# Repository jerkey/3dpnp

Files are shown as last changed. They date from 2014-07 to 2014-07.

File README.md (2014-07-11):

rotatorbracket.scad is for mounting a 6403R200 hollow-shaft motor on the right side of a 2014 type a machine http://typeamachines.com
the bracket fits on the bottom edge of the circuitboard using 18mm long screws to replace the original screws that held the board in place.
the Vcc Out connector can't be used as the connector is covering it up.  solder to the back of the board if you need Vcc out.

a 3.15mm tube is shoved through the motor and fits through the hole of the bracket, where a vacuum hose is attached.  A piece of heat shrink or two go around the lower end of the tube so that the vacuum pick and place needle can be shoved on and stays centered.

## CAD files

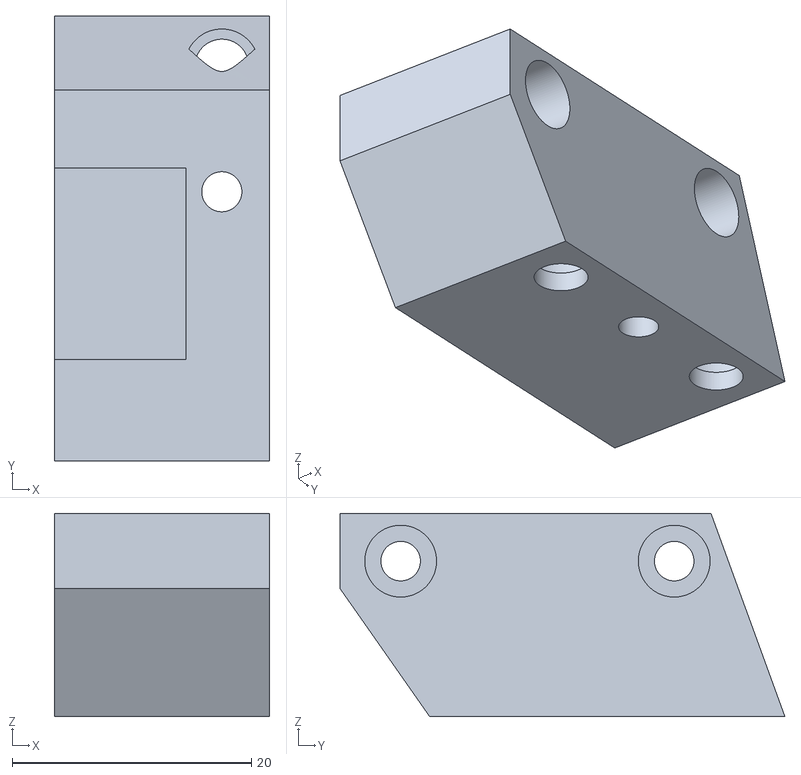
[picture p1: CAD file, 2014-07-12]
rotatorbracket.stl
18.0 x 37.2 x 17.0

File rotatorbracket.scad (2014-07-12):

$fn=100;
pipeDia = 3.35;
blockY = 33;
blockZ = 17;
blockX = 18;
motorCenterX = 14; // X line of motor posts and shaft
motorOffsetY = 6; // move the motor +Y this much relative to center

boardScrewSpacing = 25.4*0.9; // screws are 0.9" apart
screwHoleDia = 3.3; // M3 screw thread clearance tunnel
screwHeadDia = 6; // M3 screw head clearance tunnel

difference() {
  translate([0,blockY/-2,0]) cube([blockX,blockY+motorOffsetY,blockZ]);
  translate([motorCenterX,motorOffsetY,-0.1]) cylinder(r = pipeDia/2, h = blockZ+.2); // pipe hole
  translate([motorCenterX,21/2+motorOffsetY,-0.1]) cylinder(r = 4.5/2, h = 2); // motor nub holes (drill to 4.3mm)
  translate([motorCenterX,-21/2+motorOffsetY,-0.1]) cylinder(r = 4.5/2, h = 2);
  translate([motorCenterX,21/2+motorOffsetY,1.7]) cylinder(r = 6.2/2, h = 6); // motor nub larger part
  translate([motorCenterX,-21/2+motorOffsetY,1.7]) cylinder(r = 6.2/2, h = 6);
  translate([motorCenterX,21/2+motorOffsetY,1.7+5.9]) cylinder(r1=6.2/2, r2=0, h = 6); // motor nub conical top (for printability)
  translate([motorCenterX,-21/2+motorOffsetY,1.7+5.9]) cylinder(r1=6.2/2, r2=0, h = 6);
  #translate([-0.1,blockY/2-2,blockZ]) rotate([-70,0,0]) cube([blockX+0.2,blockY+motorOffsetY,blockZ]);
  #translate([-0.1,-9,0]) rotate([125,0,0]) cube([blockX+0.2,blockY+motorOffsetY,blockZ]);

  translate([-0.1,-8,13-4]) cube([11.1,16,8.1]); // Vout connector with nothing plugged into it
  translate([-0.1,boardScrewSpacing / 2,13]) rotate([0,90,0]) cylinder(r = screwHoleDia/2, h = 16.2); // screw body hole
  translate([-0.1,-boardScrewSpacing / 2,13]) rotate([0,90,0]) cylinder(r = screwHoleDia/2, h = 16.2);
  translate([10,boardScrewSpacing / 2,13]) rotate([0,90,0]) cylinder(r = screwHeadDia/2, h = 16.2); // screw head clearance
  translate([10,-boardScrewSpacing / 2,13]) rotate([0,90,0]) cylinder(r = screwHeadDia/2, h = 16.2);
}

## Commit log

2014-07-11 first commit of rotatorbracket
    [rotatorbracket.scad, rotatorbracket.stl]
2014-07-12 move motor in the Y dimension, correct board screw spacing
    [rotatorbracket.scad]
2014-07-12 increase Vout connector relief, remove excess material
    [rotatorbracket.scad, rotatorbracket.stl]
